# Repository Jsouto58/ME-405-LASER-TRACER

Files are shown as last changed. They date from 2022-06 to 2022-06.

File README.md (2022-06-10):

# ME-405-LASER-TRACER
## Created by Jake Souto and Harrison Power

###### Project:
  The objective for this project was to create a 2½ degree pen plotter with the challenge of making both dimensions non-linear. For our project we chose to control a laser pointer across two radial dimensions taking a long exposure photo of the laser path to “record the drawing”. In addition to this, we plot the curve that the machine is drawing on the computer in real time. Below is our final design as well as some of the drawings we made with it. A video of it functioning can be found [here](Video.mov).
  
  <p align="center">
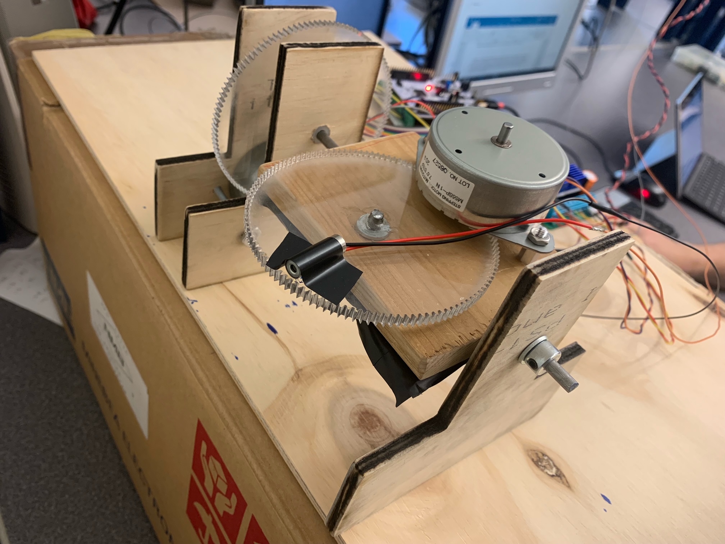
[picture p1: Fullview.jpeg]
  
  </p>
   <p align="center">
    
  </p> 

###### Chassis:
  The chassis of our machine is functional for its purpose but has room for improvements. The supports of our chassis are laser cut wooden T’s which holds the vertical motor and the axles for the gears and platform. The acrylic laser cut gears are fundamental to this project as they gear up our stepper motor 10-1 allowing us to achieve a resolution of 120x120 steps and greatly increase our torque. The laser cut file for the gears are avalible in our repository [here](gear.DXF). The resulting shakiness visible in our final images stem from our chassis as the T supports are not fully stable and our laser cut gears don’t perfectly mesh with the metal stepper gears.
  <p align="center">
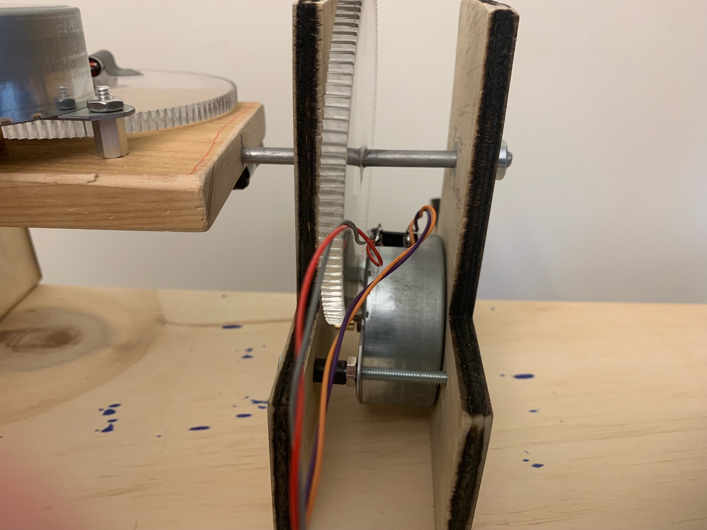
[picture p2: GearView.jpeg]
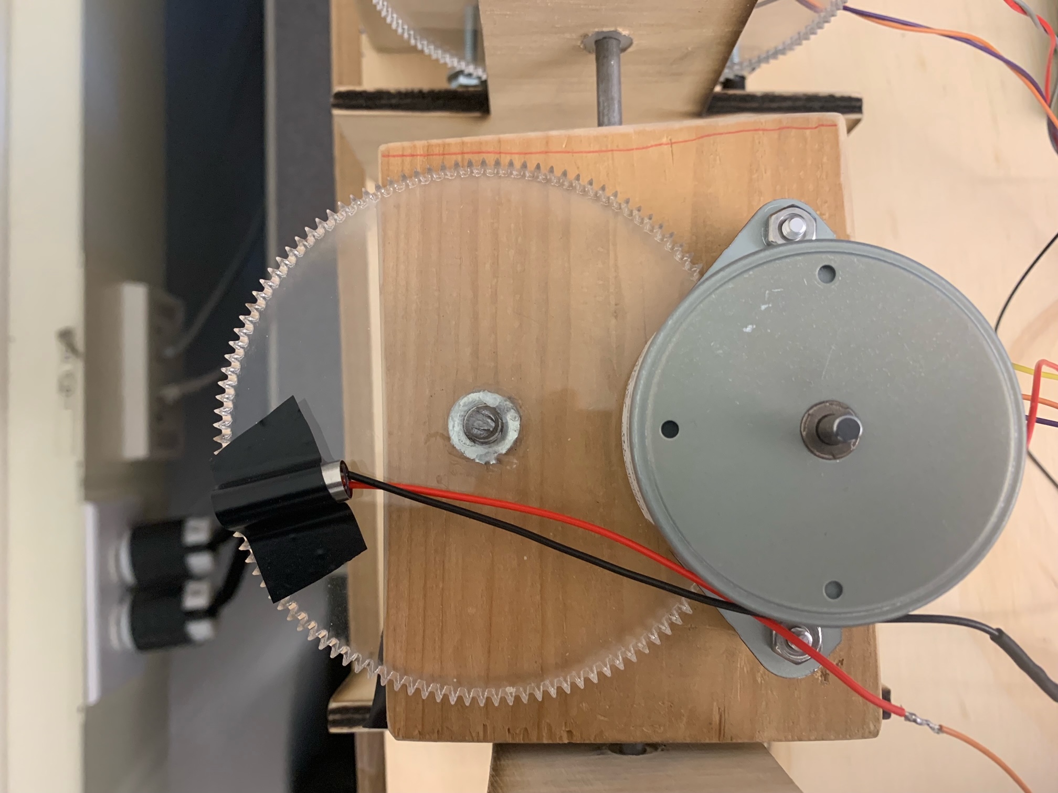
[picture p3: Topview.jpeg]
   
  </p> 

###### Hardware:
The Board we used for this project is a Nucleo L476RG which interfaced serially with a TMC 4210 stepper motor IC, which gave commands to the TMC 2208 motor driver. The TMC 4210 and the TMC 2208 were pre-assembled on a custom PCB board which handled the connections between the two devices. The Nucleo was connected to this board and the motors as shown in the diagram below. 
<p align="center">
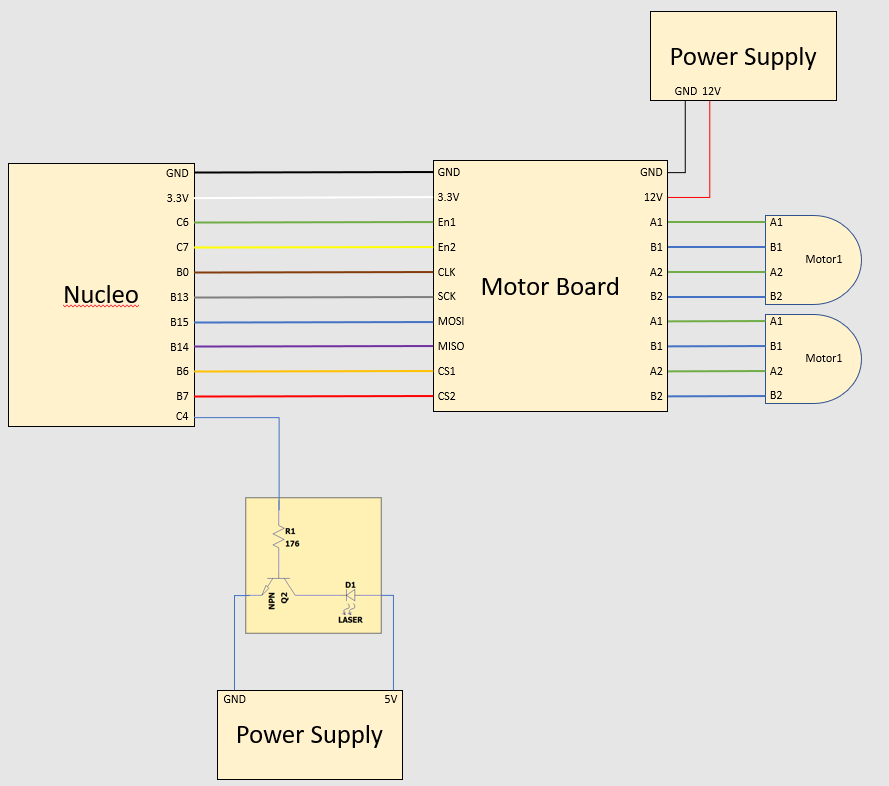
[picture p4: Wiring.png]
   
  </p>
The TMC 2208 chips had an on board current limiting potentiometer that we had to adjust manually. This was set by measuring the voltage across the vref pin and ground, and adjusting the potentiometer until the voltage read 0.7 V. The motors we used were 48 step per rotation / 7.5 degree per step four wire stepper motors. We unsoldered the circuit on the face of the motor to manually solder wired directly to the pins to more easily interface with the motors.
<p align="center">
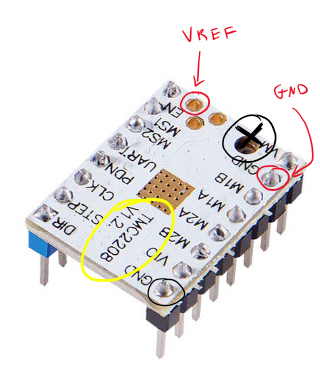
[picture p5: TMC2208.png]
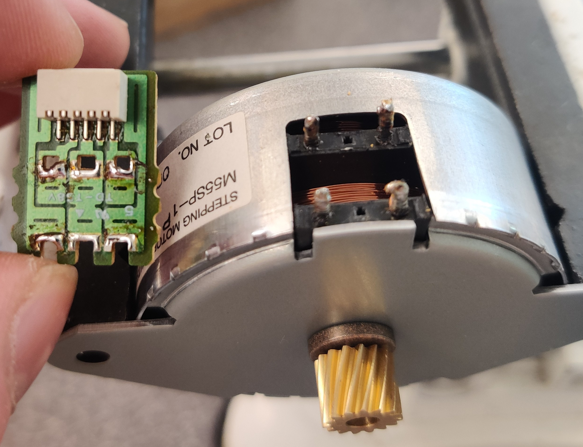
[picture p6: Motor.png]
   
  </p>

###### Movement Calculations:
To convert the x,y coordinates to radial coordinates that we could write to our stepper motors we used what is called the Newton-Raphson algorithm. This algorithm consecutively approximates any given solution to an equation using the formula below. 

$$\begin{equation}
\frac{df^{-1}}{dθ} = 
  \begin{bmatrix}
    \frac{1}{rsec^2(θ1)} & 0 \\
    0 & \frac{1}{rsec^2(θ2)}
  \end{bmatrix}
\end{equation}$$

$$\begin{equation}
x_{n+1} =  x_n - 
  \begin{bmatrix}
    \frac{1}{rsec^2(θ1)} & 0 \\
    0 & \frac{1}{rsec^2(θ2)}
  \end{bmatrix}
  \begin{bmatrix}
    rtan(θ1)\\
    rtan(θ2)
  \end{bmatrix}
\end{equation}$$

This equation iterated through until the difference between the next step and the current one is less than some threshold; we know that the calculated thetas correspond to the desired x,y coordinates. Implementing this function into python and generating thetas for a simple circle we were able to generate this gif to prove that our equation was correct for our implementation. 
<p align="center">
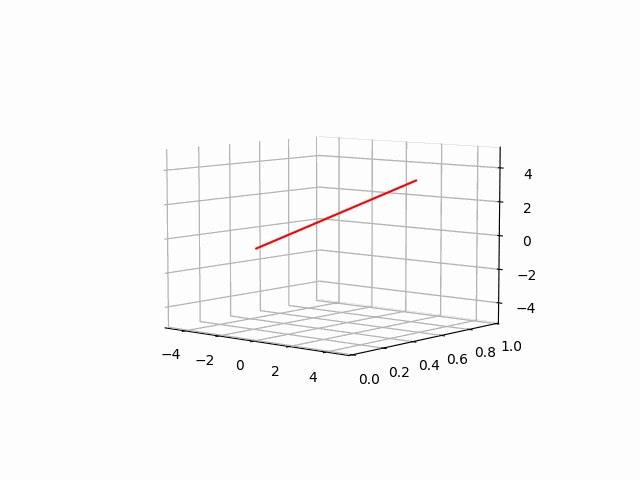
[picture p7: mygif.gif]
   
  </p>

###### Code:
The main executable for our project is [Wrapper.py](Wrapper.py). Wrapper.py reads the hpgl file, deconstructs the instructions into a set of coordinates, runs each coordinate through the Newton-Raphson, interpolates the data, and initializes the tasks all upon start-up. There are three tasks: getActual() updates a share with the actual position of the motor received from the TMC4210, motorCheck() evaluates if a new location should be sent based on if the current position matches the target location and computerSend() which sends the actually position of the stepper to the computer to graph in real time. The tasks are outlined in the left figure below.
<p align="center">
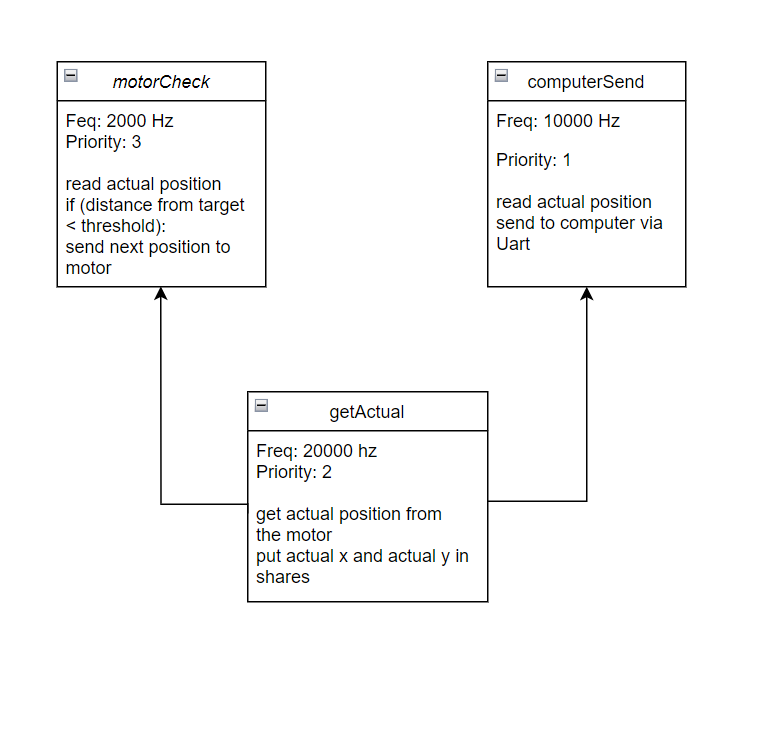
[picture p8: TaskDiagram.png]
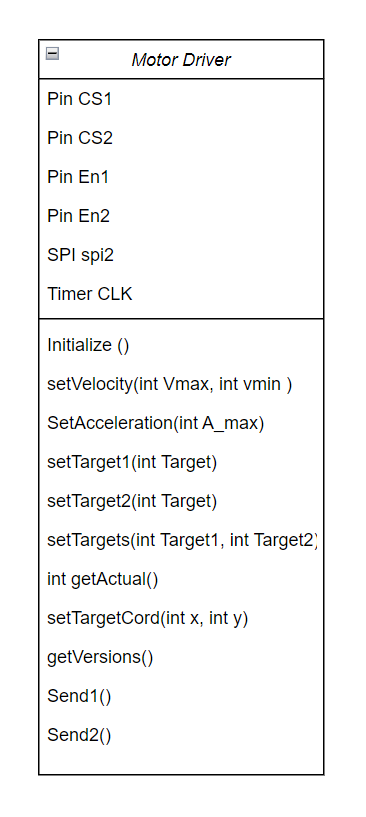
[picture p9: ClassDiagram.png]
   
  </p> 
  
The [StepperClass.py](StepperClass.py) is a library of the Stepper class which initializes and communicates to the TMC4210 chip. A single instantiation of the Stepper is able to communicate to control two motors which is documented above in the image on the right. In order to get the stepper motors to move many of the TMC registers needed to be initialized as detailed in the datasheet for the TMC4210. Some of the values in the register are concretely defined needing to be set to certain values in order to function. However, some registers controlled internal settings that varied depending on the implementation notably, the speed settings. All of the presets we used can be found in our StepperClass.py.

The [Bell.py](Bell.py) is a separate executable to be run on an external computer not the Nucleo. This file reads the serial port connected to the Nucleo and receives the actual motor position. It decodes the serial communication into (x,y) coordinates and creates and updating graph that traces the coordinates in real time.

###### Instructions:
Setup the device facing a wall with ample space below and above the machine. Ensure the laser is pointing appropriately in the center of the Canvas then turn on the power supply to the stepper motors. Apply 5V to the laser pointer circuit and the hardware is set up.

For the software download the code from the git repository. There are three important programs, StepperClass.py, Wrapper.py, cotask.py, task_share.py and Bell.py. The Bell.py file stays on the computer while all of the other files will be installed via Thonny onto the Nucleo. Additionally, an hpgl file of the desired path should be installed onto the Nucleo as well. Once all the files are installed, edit Wrapper to ensure that it correctly opens the desired hpgl file. Connect the Nucleo to the desktop and run the Bell.py program (make sure it has the correct com port for your computer) which will wait for the serial input from the Nucleo. Run the Wrapper.py file from the Nucleo and the machine will begin to draw the path and update the live tracker on the computer.

###### Reflection:
If we were to undertake this project again we would improve upon a few things. Primarily the major restraint keeping us from drawing very clean lines is the chassis. The chassis design was not sturdy and allowed the whole device to vibrate and shake. The gears being of a laser cut material ended up a little smaller than the CAD drawing preventing the gear from meshing perfectly with the motor gear. Overall this oversight allowed our machine to vibrate during operation causing the shakiness seen in the final drawings.

On the software side a large issue encountered by many teams was a memory error. This was caused by the interpolated Newton- Raphson taking up too much of the Nucleo’s memory, causing it to crash. If we did this again we would store and calculate all of the coordinate points on a computer and send individual coordinates to the Nucleo allowing us to run very large images with a high level of accuracy.

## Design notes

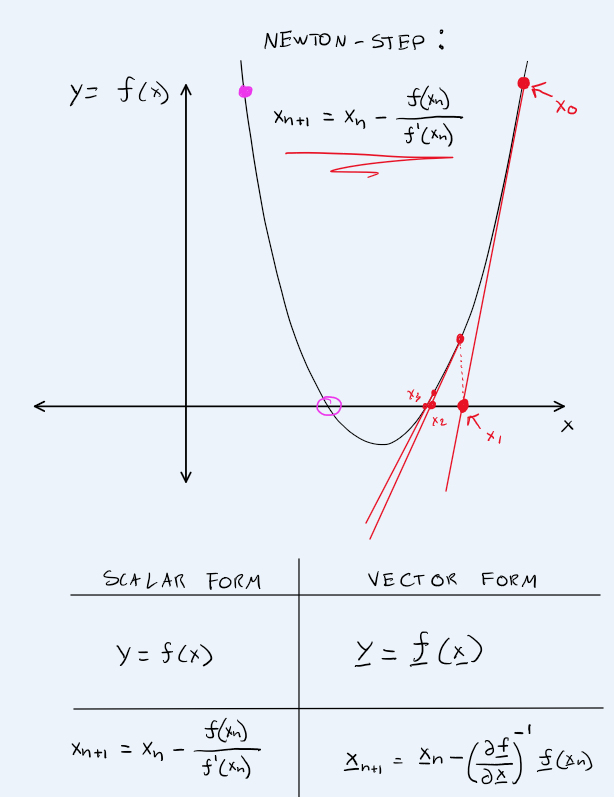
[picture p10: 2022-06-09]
Newtonstep.png

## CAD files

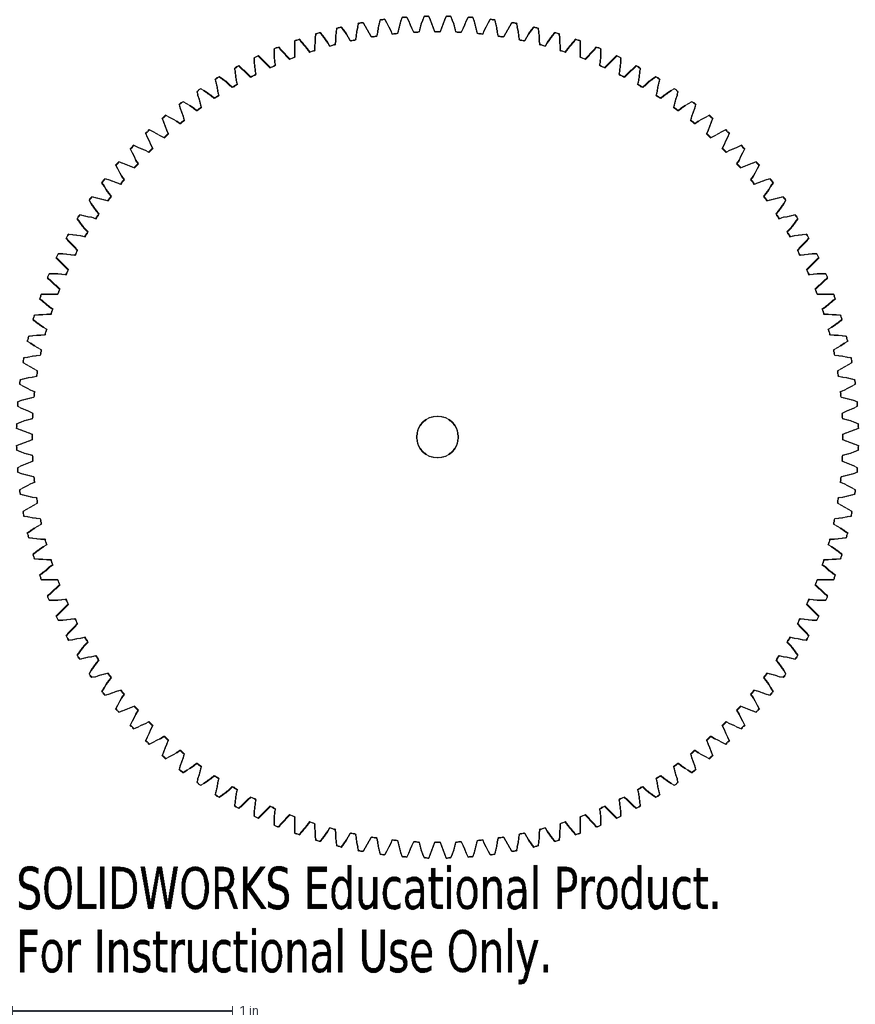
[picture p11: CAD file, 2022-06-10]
gear.DXF
SOLIDWORKS Educational Product.
For Instructional Use Only.

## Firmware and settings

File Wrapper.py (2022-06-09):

#import La
from ulab import numpy
import math
import pyb
from pyb import UART
from pyb import Pin
import micropython
import StepperClass
import gc
import cotask
import task_share
pyb.repl_uart(None)

def g(x, theta):
    r = 1
    X = numpy.array(x)
    Theta = numpy.array([r*math.tan(theta[0]*math.pi/180), r*math.tan(theta[1]* math.pi/180)])
    return X -Theta
    
def dg_theta(theta):
    r = 1
    return(numpy.array([[-r*math.pow(1/math.cos(theta[0]*math.pi/180), 2), 0], [0, -r*math.pow(1/math.cos(theta[1]*math.pi/180), 2)]]))
    
def NewtonRaphson(fcn, jacobian, guess, thresh):
    steps = 1
    while (abs(fcn(guess)[0]) > thresh or abs(fcn(guess)[1]) > thresh):
        math = guess - numpy.dot(numpy.linalg.inv(jacobian(guess)),fcn(guess))
        guess = math
        steps += 1
    return guess

#---------------------------------------------
def motorsend():
    i = 3
    current = 2
    while i < len(datax):
        iterations.put(i)
        if datax[i] == "PU":
            LASER.low()
            i+=1
            yield(0)
        elif datax[i] == "PD":
            LASER.high()
            i+=1
            yield(0)
        else:
            xs = numpy.linspace(datax[current],datax[i],5)
            ys = numpy.linspace(datay[current],datay[i],5)
            gc.collect ()
            for j in range(len(xs)):
                TargetX.put(xs[j])
                TargetY.put(ys[j])
                motor.SetTargets(xs[j],ys[j])
                yield(0)
            current = i
            i+= 1

def motorCheck():
    while True:
        actx = ActX.get()
        acty = ActY.get()
        if abs(actx - TargetX.get()) < .5 and abs(acty - TargetY.get()) < .5 :
           next(motorsend)
        yield(0)



def computerSend():
    while True:
        actx = ActX.get()
        acty = ActY.get()
        uart.write(str(actx) +":"+ str(acty) +"\n")
        yield(0)
        
def getActual():
    while True:
        actx,acty = motor.GetActual()
        ActX.put(actx)
        ActY.put(acty)
        yield(0)
#---------------------------------------------------------------------------------------

# run this on startup
if __name__ == "__main__":
    pyb.repl_uart(None)
    print("start")
    uart = UART(2,115200)
    uart.init(115200, bits=8, parity=0, stop=1)
    micropython.alloc_emergency_exception_buf(100)
    LASER = Pin("C4",mode=Pin.OUT, value=0)
    ActX = task_share.Share ('f', thread_protect = False, name = "X Position")
    ActY = task_share.Share ('f', thread_protect = False, name = "Y Position")
    TargetX = task_share.Share ('f', thread_protect = False, name = "TargetX")
    TargetY = task_share.Share ('f', thread_protect = False, name = "TargetY")
    iterations= task_share.Share ('i', thread_protect = False, name = "iterations")
    q0 = task_share.Queue ('f', 4, thread_protect = False, overwrite = False, name = "Queue 0")
    ActX.put(0)
    ActY.put(0)
    TargetX.put(0)
    TargetY.put(0)
    motorsend = motorsend()
    print("actuals", ActX.get(), ActY.get())
    print("Target", TargetX, TargetY)
    pyb.repl_uart(None)
    f = open("Diamond.hpgl","r")
    Line = f.readline()
    List=Line.split(";")
    guess = [0,0]
    scalar = 120
    datax = []
    datay = []

    for command in List:
        if command == "IN":
            print("IN")
            motor = StepperClass.Stepper()
        elif "PU" in command:
            datax.append("PU")
            datay.append("PU")  
            temp = command.replace("PU","")
            temp = temp.split(",")
            if len(temp) != 1:
                for i in range(0, len(temp)-1,2):
                    X = [int(temp[i])/scalar,int(temp[i+1])/scalar]
                    answer = NewtonRaphson(lambda theta : g(X, theta), dg_theta, guess,  .1)
                    datax.append((answer[0]))
                    datay.append((answer[1]))
                    
        elif "PD" in command:
            datax.append("PD")
            datay.append("PD")  
            temp = command.replace("PD","")
            temp = temp.split(",")
            if len(temp) != 1:
                for i in range(0, len(temp)-1,2):
                    X = [int(temp[i])/scalar,int(temp[i+1])/scalar]
                    answer = NewtonRaphson(lambda theta : g(X, theta), dg_theta, guess,  .1)
                    datax.append((answer[0]))
                    datay.append((answer[1]))                               
        else:
            print("NA")
            
    motorcheck = cotask.Task (motorCheck, name = 'motorcheck', priority = 3, period = 500, profile = True, trace = False)
    computersend = cotask.Task (computerSend, name = 'computersend', priority = 1, period = 100, profile = True, trace = False)
    getactual = cotask.Task (getActual, name = 'getactual', priority = 2, period = 50, profile = True, trace = False)
    cotask.task_list.append (motorcheck)
    cotask.task_list.append (computersend)
    cotask.task_list.append (getactual)
    gc.collect ()

    while True:
        cotask.task_list.pri_sched ()
        gc.collect ()
#---------------------------------------------------------------------------------------

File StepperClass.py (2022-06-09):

import pyb
from pyb import Pin
from pyb import SPI
import ustruct


class Stepper:
    def __init__(self):
        self.En1 = Pin("C6",mode=Pin.OUT, value=0)
        self.En2 = Pin("C7",mode=Pin.OUT, value=0)
        self.cs1 = Pin('B6', mode=Pin.OUT, value=1)
        self.cs2 = Pin('B7', mode = Pin.OUT, value = 1)
        self.PB0 = Pin('B0', mode=Pin.OUT_PP)
        
        self.tim = pyb.Timer(1,period = 3, prescaler = 0)
        self.clk = self.tim.channel(2, pin = self.PB0, mode = pyb.Timer.PWM, pulse_width = 2)
        self.spi = SPI(2, SPI.CONTROLLER, baudrate=600000, polarity=1, phase=1,firstbit=SPI.MSB)
        
        #Enabling Stepper Driver
        ba = bytearray([0b01101000,0b00000000,0b00000000,0b00100000])
        self.Send1(ba)
        self.Send2(ba)
        
        #Set Velocities
        self.SetVelocity(0b00110000,0b11111111)
        
        #Set Pulse/Ramp Div
        ba = bytearray([0b00011000,0b00000000,0b01110111,0b00000000])
        self.Send1(ba)
        self.Send2(ba)
        
        #Set Amax
        self.SetAcceleration("None")
        
        #Set Ramp Mode
        ba = bytearray([0b00010100,0b00000000,0b00000011,0b00000000])
        self.Send1(ba)
        self.Send2(ba)
        
        #Set Current Pos
        ba = bytearray([0b00000010,0b00000000,0b00000000,0b00000000])
        self.Send1(ba)
        self.Send2(ba)
        
    def SetVelocity(self,Vmin, Vmax):
        #Enter Numbers in form of bits
        bamin = bytearray([0b00000100,0b00000000,0b00000000,Vmin])
        bamax = bytearray([0b00000110,0b00000000,0b00000000,Vmax])
        self.Send1(bamin)
        self.Send1(bamax)
        self.Send2(bamin)
        self.Send2(bamax)
        
    def SetAcceleration(self,Amax):
        #Amax = 1040
        #Pmul = 128
        #Pdiv = 2**4... 1 register
        #q = .98
        ba = bytearray([0b00001100,0b00000000,0b00000000,0b11110101]) #Amax
        self.Send1(ba)
        self.Send2(ba)
        
        ba = bytearray([0b00010010,0b00000000,0b11110100,0b00000101]) #Pmul 244 / Pdiv 2
        self.Send1(ba)
        self.Send2(ba)
        
    def LimitSwithes(self):
        pass

    def SetTarget1(self, Target):
        SmallRotation = Target * 10
        Steps = round((384 * (SmallRotation/360)))
        ba2 = Steps.to_bytes(3,"big")
        ba = bytearray(([0b000000000, ba2[0], ba2[1],ba2[2]]))
        self.Send1(ba)

        
    def SetTarget2(self, Target):
        SmallRotation = Target * 10
        Steps = round((384 * (SmallRotation/360)))
        ba2 = Steps.to_bytes(3,"big")
        ba = bytearray(([0b000000000, ba2[0], ba2[1],ba2[2]]))
        self.Send2(ba)
    
    def SetTargets(self, x, y):
        self.SetTarget1(x)
        self.SetTarget2(y)
    
    def GetActual(self):
        ba = bytearray([0b00000011,0b00000000,0b00000000,0b00000000])
        data = self.Send1(ba)     
        if data[1]>> 7 == 1:
            Steps = bytearray([0b11111111, data[1], data[2],data[3]])
        else:
            Steps = bytearray([0b00000000, data[1], data[2],data[3]])
        Steps = ustruct.unpack(">l", Steps)[0]
        SmallRotation = ((int(Steps)/384) * 360)
        Target1 = SmallRotation/10

        ba = bytearray([0b00000011,0b00000000,0b00000000,0b00000000])
        data = self.Send2(ba)
        if data[1]>> 7 == 1:
            Steps = bytearray([0b11111111, data[1], data[2],data[3]])
        else:
            Steps = bytearray([0b00000000, data[1], data[2],data[3]])
        Steps = ustruct.unpack(">l", Steps)[0]
        SmallRotation = ((int(Steps)/384) * 360)
        Target2 = SmallRotation/10
        return(Target1,Target2)
        
    def GetVersions(self):
        print("Chip 1")
        ba = bytearray([0b01110011,0b00000000,0b00000000,0b00000000])
        data = self.Send1(ba)
        for idx,byte in enumerate(data): print(f"b{3-idx}: {byte:#010b} {byte:#04x}")
        print("Chip 2")
        data = self.Send2(ba)
        for idx,byte in enumerate(data): print(f"b{3-idx}: {byte:#010b} {byte:#04x}")
        
    def Send1(self,byte):
        self.cs1.low()
        data = self.spi.send_recv(byte)
        self.cs1.high()
        return data
    
    def Send2(self,byte):
        self.cs2.low()
        data = self.spi.send_recv(byte)
        self.cs2.high()
        return data
   
#Motor = Stepper()
#Motor.GetVersions()
#Motor.GetActual()
#Motor.SetTarget(180)

#Motor.SetTargets(0,3)
#pyb.delay(1000)
#Motor.GetActual()

 

    
